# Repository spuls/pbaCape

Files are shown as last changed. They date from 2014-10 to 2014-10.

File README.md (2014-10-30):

pbaCape
=======

BeagleBone Cape for pba ("Platz-Beregnungs-Anlage")

For software see https://github.com/fknittel/pba

## TestBoard
For testing the basic circuit a test layout was developed. It was soldered together and used with one original relay (same as used for the "real" thing).

## Prototype RC1
The RC1 schematics were send of for PCB manufacturing. The bare board was soldered manually. The prototype is still used for the "real" thing. But:
- Some resistor values were choosen borderline. Only 4 out of 6 outputs worked as advertised. (Values corrected in V05.sch)
  Wrong relay behaviour can be seen here: https://www.youtube.com/watch?v=9P7xhbd6JEQ 
  Correctly it should be: https://www.youtube.com/watch?v=5yiceOrfvFM 
- Some GPIOs (P8_39, 41, 43, 45) that were chosen first interfered with "boot"-pins of the BeagelBone. Thus, the board would not boot properly.
  These were manually corrected via wire bridges to be P8_17, 18, 28 and 30 respectively. (Also corrected in V05.sch)
- There is no internet connection (currently). Thus, no time information is available. A real time clock (RTC) was needed. It was manually soldered. 
  (Not yet corrected in schematics.)

## Code
The code here is only for simple testing purposes. It uses PyBBIO (https://github.com/alexanderhiam/PyBBIO/wiki).

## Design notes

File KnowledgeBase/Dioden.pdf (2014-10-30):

ANGEWANDTE ELEKTRONIK | DIODEN | SEITE 1

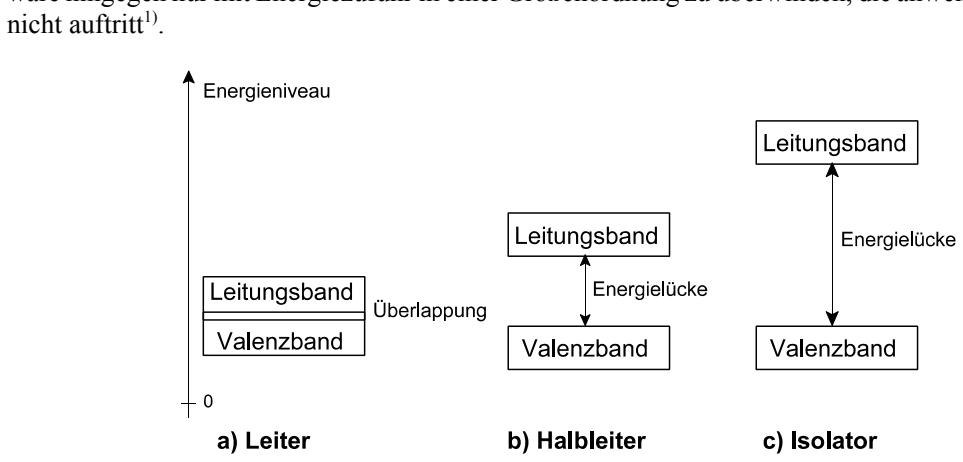
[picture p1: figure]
nicht auftritt¹⁾.

1: Oder – falls doch – zerstörende Wirkungen hätte (Durchschlagen, Durchbrennen).

## 1. Dioden

### 1.1 Grundlagen

Leiter – Halbleiter – Isolatoren
Ein elektrischer Strom kann nur dann fließen, wenn Ladungsträger zur Verfügung stehen. Der elementare Ladungsträger ist das Elektron. Elektronen sind jene Elementarteilchen, die die Kerne der Atome umkreisen. Sind alle Elektronen in den Atomen gebunden, so stehen keine Ladungsträger zur Verfügung, um Strom leiten zu können. Ein solcher Stoff stellt einen idealen Isolator (Nichtleiter) dar. Indem man Energie aufwendet, ist es möglich, Elektronen aus dem Atom herauszulösen und somit als freie Ladungsträger verfügbar zu machen. Das betrifft jene Elektronen, die sich in der der äußeren Schale befinden und die die Bindungen zwischen benachbarten Atomen bewirken (Valenzelektronen). Die Stoffe unterscheiden sich darin, wieviel Energie zugeführt werden muß, um Valenzelektronen freizusetzen. Hierbei gibt es keinen kontinuierlichen Übergang, sondern Bereiche (Bänder), denen verschiedene Energieniveaus zugeordnet sind (Abb. 1.1). Beim Leiter überlappen sich beide Bänder, so daß auch ohne besondere Energiezufuhr stets freie Elektronen zur Verfügung stehen. Bei Halbleitern und Isolatoren sind die Bänder voneinander entfernt (Energielücke). Um Elektronen aus dem Valenzband herauszulösen und in das Leitungsband zu überführen, ist diese Energielücke durch Energiezufuhr zu überwinden. Die schmale Energielücke der Halbleiter kann überwunden werden. Die breite Energielücke der Isolatoren wäre hingegen nur mit Energiezufuhr in einer Größenordnung zu überwinden, die anwendungspraktisch

Abb. 1.1 Valenzband: das Elektron befindet sich in der äußeren Schale und krese um den Atomkern. Leitungsband: das Elektron ist nicht mehr im Atom gebunden, sondern frei beweglich. Es steht somit zur Verfügung, um Strom zu leiten.

Eigenleitung
Die uns interessierenden Halbleitermaterialien sind Kristallstrukturen. Ein absolut reiner Halbleiterkristall, z. B. ein Stück Reinstsilizium, leitet bei tiefen Temperaturen praktisch keinen Strom. Es stehen keine Ladungsträger zur Verfügung, da alle Elektronen in den Atomen des Kristallgitters gebunden sind. Wärme oder Licht versetzen die Atome in Schwingungen. Dadurch werden einige Elektronen aus dem Verband herausgelöst, so daß Strom fließen kann. Die herausgelösten Elektronen hinterlassen buchstäblich "Löcher" (Holes) in den Kristallbindungen. Diese sind logischerweise Träger

ANGEWANDTE ELEKTRONIK | DIODEN | SEITE 2

einer positiven Ladung. Ein solches Loch kann von einem Elektron besetzt werden, das dann seinerseits ein Loch hinterläßt. Den Vorgang, daß ein Elektron eine Loch-Position besetzt, nennt man Rekombination.

Obwohl ein Loch (andere Bezeichnungen: Fehlstelle, Störstelle, Defektelektron) nichts Gegenständliches ist, kann man es als Träger positiver Ladung ansehen und mit den entsprechenden Ladungsträger-Kennwerten rechnen. So entsprechen Masse und Ladungsmenge eines Loches der eines Elektrons (nur hat die Ladungsmenge ein umgekehrtes Vorzeichen). Elektronen fließen von Minus nach Plus, Löcher von Plus nach Minus. Die Bewegungsgeschwindigkeit von Löchern ist aber viel geringer als die von Elektronen (das ist die physikalische Ursache dafür, daß man für NPN-Transistoren weniger Silizium braucht als für PNP-Transistoren mit vergleichbaren Kennwerten).

Dotierung
Um mit Halbleitern Gleichricht- und Verstärkerwirkung zu erbringen, ist die Eigenleitung nicht ausreichend. Man muß vielmehr den Leitungsmechanismus gezielt beeinflussen. Dies erreicht man durch Beimischungen von Atomen anderer Wertigkeit (Dotierung). Hat ein solches Atom eine höhere Wertigkeit, so können nicht alle seine Bindungselektronen in den Kristallverband eingebaut (und somit neutralisiert) werden. Somit ist ein Überschuß an Elektronen vorhanden, der verfügbar ist, um Strom zu leiten (Elektronen- oder N-Leitung). Hat ein solches Atom hingegen eine geringere Wertigkeit, so fehlen an den Bindungsstellen des Kristalls Elektronen. Somit ist ein Überschuß an Löchern vorhanden, der ebenfalls zur Stromleitung nutzbar ist (Löcher- oder P-Leitung). Eine Dotierung, die einen Elektronenüberschuß erzeugt, heißt Donator-Dotierung, eine, die einen Überschuß an Löchern erzeugt, Akzeptor-Dotierung. Die Ladungsträger, die infolge der Dotierung vorherrschen, heißen Majoritätsträger, die jeweils anderen Minoritätsträger. Bei Silizium als Halbleiter-Grundwerkstoff bestehen Donator-Dotierungen aus fünfwertigen Atomen (z. B. Antimon Sb oder Phosphor P) und Akzeptor-Dotierungen aus dreiwertigen (z. B. Bor B oder Gallium Ga). Silizium selbst ist vierwertig. Abb. 1.2 zeigt, wie durch Dotierung einer Kristallstruktur N-leitende und P-leitende Halbleiterschichten erzeugt werden. Abb. 1.3 veranschaulicht das Prinzip der Löcherleitung.

Der PN-Übergang
Ein PN-Übergang entsteht, wenn ein Stück Halbleitermaterial auf einer Seite eine Akzeptor-Dotierung und auf der anderen eine Donator-Dotierung erhält, so daß eine P-leitende Zone einer N-leitenden unmittelbar gegenübersteht (Abb. 1.4). Legt man eine Spannungsquelle mit dem Pluspol an die P-leitende Zone und mit dem Minuspol an die N-leitende, so werden die Elektronen zum Pluspol und die Löcher zum Minuspol fließen (gleichnamige Pole stoßen einander ab; die jeweiligen Majoritätsträger werden also buchstäblich aufeinander zugedrückt). Im eigentlichen Übergangsbereich treffen Elektronen und Löcher aufeinander und rekombinieren. Es fließt also tatsächlich ein Strom. Legt man hingegen die Spannungsquelle mit dem Pluspol an die N-leitende Zone und mit dem Minuspol an die P-leitende, so werden die Majoritätsträger förmlich zu den Anschlüssen der Spannungsquelle hingesaugt (ungleichnamige Pole ziehen einander an). Der eigentliche Übergangsbereich ist somit weitgehend frei von Ladungsträgern, so daß kein nennenswerter Strom fließen kann (Sperrschicht).

ANGEWANDTE ELEKTRONIK | DIODEN | SEITE 3

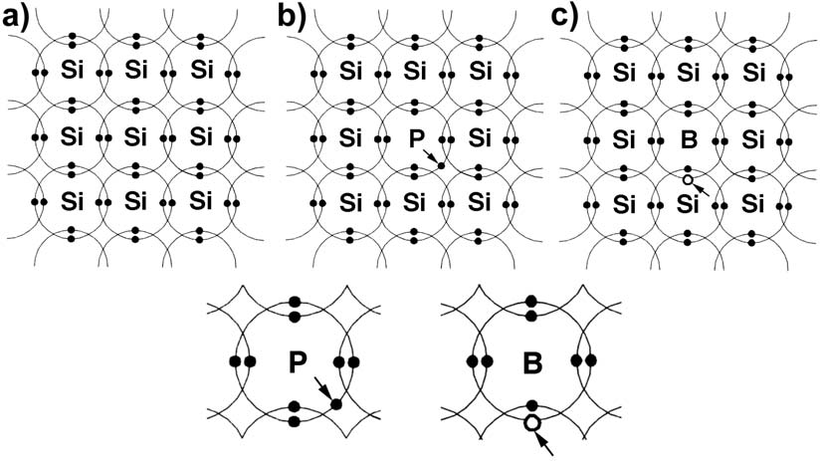
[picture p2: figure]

Abb. 1.2 Dotierung eines Halbleiterkristalls.a) ein reiner Siliziumkristall. Alle Valenzelektronen der Atome sind in Doppelbindungen (kovariante Bindungen) einbezogen. b) N-Leitung durch Einbau eines fünfwertigen Atoms (z. B. Phosphor P), c) P-Leitung durch Einbau eines dreiwertigen Atoms (z. B. Bor B).

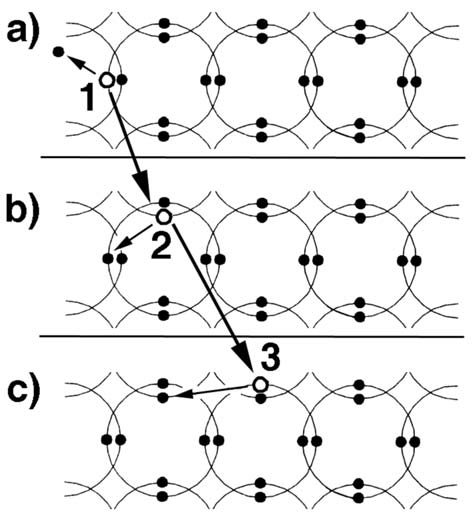
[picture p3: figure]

Abb. 1.3 Prinzip der Löcherleitung. Löcher an sich können sich nicht bewegen – auch hier sind es eigentlich die Elektronen. a), b) und c) zeigen die gleichen Atome zu verschiedenen Zeitpunkten. a) Elektron 1 verläßt seinen Platz in einer Doppelbindung; es ergibt sich das erste Loch. b) Elektron 2 verläßt seinen Platz in einer Doppelbindung und fällt gleichsam in die Position des Lochs 1 (Rekombination). c) Loch 2 wird von Elektron 3 gefüllt, das einerseits seinen Platz in einer Doppelbindung verlassen hat. Infolge dieser Elektronenbewegung scheint es so, als ob ein Loch von Postion 1 über Position 2 nach Position 3 gewandert ist.

ANGEWANDTE ELEKTRONIK | DIODEN | SEITE 4

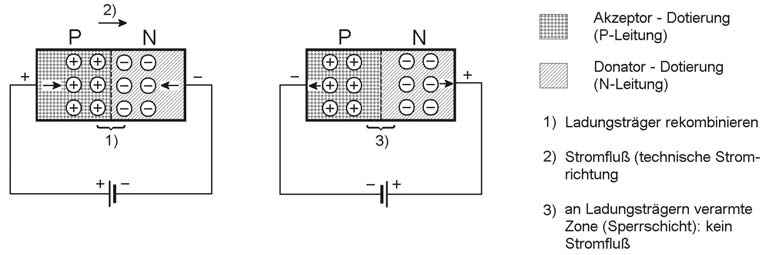
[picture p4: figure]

Abb. 1.4 Der PN-Übergang. Links: Betrieb in Durchlaßrichtung, rechts: Betrieb in Sperrichtung.

### 1.2 Dioden

Dioden sind passive Halbleiterbauelemente mit zwei Anschlüssen. Der eine Anschluß heißt Katode, der andere Anode. Die ideale Diode wirkt wie ein Schalter, dessen Stellung davon bestimmt wird, an welchem der beiden Anschlüsse das positivere und an welchem das negativere Potential anliegt:

- Liegt an der Katode eine negativere und an der Anode eine positivere Spannung an, so ist der Schalter geschlossen: die Diode ist leitend bzw. in Durchlaß- oder Flußrichtung geschaltet; es kommt ein Stromfluß zustande,
- Liegt an der Katode eine positivere und an der Anode eine negativere Spannung an, so ist der Schalter geöffnet: die Diode ist gesperrt bzw. in Sperrichtung geschaltet; es kann kein Strom fließen.

In Kurzform:

- Durchlaßrichtung (Forward Direction) = Minus an Katode, Plus an Anode.
- Sperrichtung (Reverse Direction) = Plus an Katode, Minus an Anode.

Es können verschiedene physikalische Effekte und verschiedene Materialien genutzt werden, um derart wirkende Bauelemente zu schaffen. Die meisten modernen Dioden beruhen jedoch auf dem PN-Übergang (üblicherweise als Sperrschicht bezeichnet) und auf Silizium als Basismaterial. Abb. 1.5 veranschaulicht die Grundlagen.

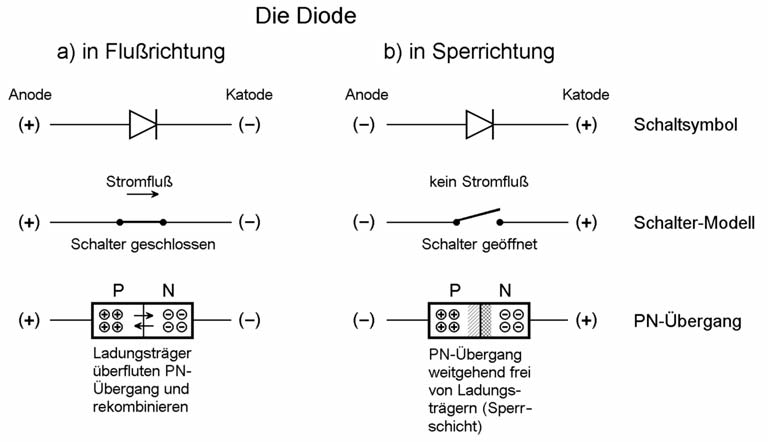
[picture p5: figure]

Abb. 1.5 Die (idealisierte) Halbleiterdiode. Die Anode ist P-leitend, die Katode N-leitend.

ANGEWANDTE ELEKTRONIK | DIODEN | SEITE 5

Die Diode in der Kennlinie
Das einfache Schaltermodell ist für die Praxis zu ungenau. Um die wesentlichen Einzelheiten zu erkennen, müssen wir uns die Strom-Spannungs-Kennlinie der Diode ansehen (Abb. 1.6).

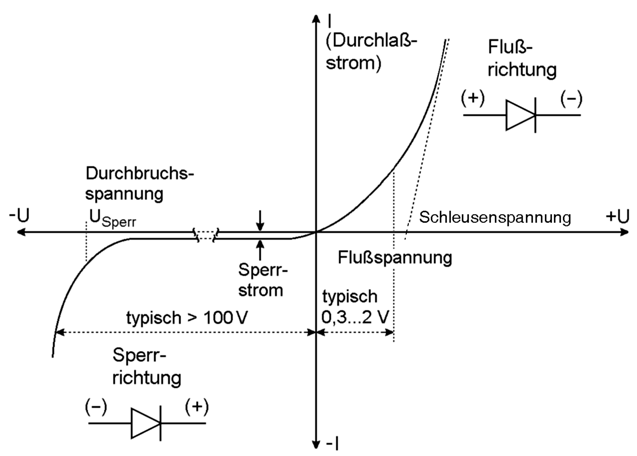
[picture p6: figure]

Abb. 1.6 Diodenkennlinie.

Gleichung der Diodenkennlinie:

I | I | e | Ie D | S

U
nU
S

U
T | T nU =· | -

æ

è

ç
ç

ö

ø

÷
÷ ≈· · | · 1

IS = Sperrsättigungsstrom.

Temperaturspannung U kT
q T =

Bei Zimmertemperatur gilt:

- bei 20 °C: UT . 25 mV,
- bei 25 °C: UT . 26 mV.
k = Boltzmannkonstante 138 10 23 , · - Ws
K

T = Temperatur in K

q = Elementarladung e = 0,16021892 •10⁻¹⁸ C

n = Anpassungsfaktor (Erfahrungswert).

ANGEWANDTE ELEKTRONIK | DIODEN | SEITE 6
| Spannungsbereich | n
Germanium | – | 1
Silizium | U # US | 2
Silizium | U > US | 1

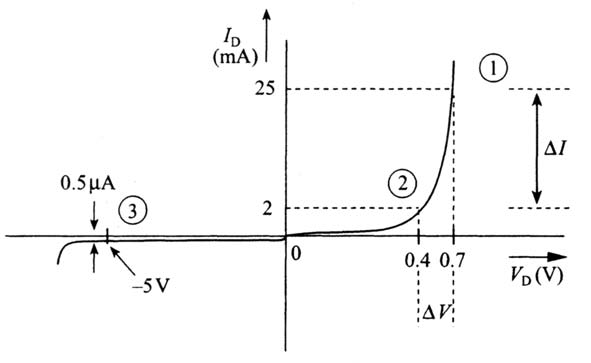
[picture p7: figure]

Abb. 1.7 Der statische Widerstand der Diode.

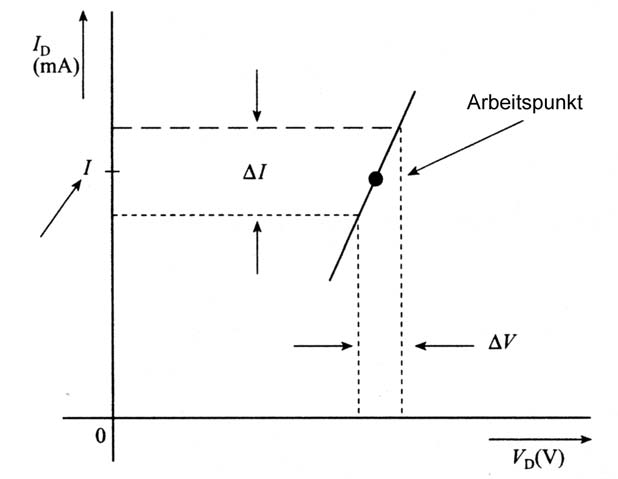
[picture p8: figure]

Abb. 1.8 Der differentielle Widerstand (Wechselstromwiderstand). Er gilt für kleine Änderungen von Spannung und Strom.

Differentieller Widerstand :
dI
dU

e
kT

## Ie S

eU
kT = ··

·

ANGEWANDTE ELEKTRONIK | DIODEN | SEITE 7

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
T = | = | ·
·

≈ ·

1

r

V
I d ≈

0 026 ,

Das entspricht einem differentiellen Leitwert von 38,5 S • I.

Für einen gegebenen Durchlaßstrom IF gilt somit:

- Widerstand = 26 Ω • mA : IF.
- Leitwert = 38,5 mS/mA • IF.

Das entspricht einer Zunahme der Flußspannung um 18 mV bei Verdoppelung und um 60 mV bei Verzehnfachung des Durchlaßstroms (also je Oktave bzw. Dekade).

Temperaturabhängigkeit (Silizium):

- für je 1° Temperaturanstieg fällt die Flußspannung um 2 mV,
- für je 10° Temperaturanstieg verdoppelt sich der Sperrstrom.

Die Durchlaßrichtung
Wenn, von Wert 0 an beginnend, die Spannung an der Anode – bezogen auf die Katode – mehr und mehr positiv wird, fließt zunächst ein nur geringer Strom. Erst nach Überschreiten eines gewissen Spannungswertes Ud steigt die Stromstärke steil an. Dabei nimmt der Spannungsabfall über der Diode kaum zu. Den Wert Ud bezeichnet man als Durchlaß-, Fluß- oder Kniespannung der Diode. Bei geringen Spannungen und Strömen entspricht die Kennlinie in guter Näherung einer Exponentialfunktion.

Die Sperrichtung
Wenn, von Wert 0 an beginnend, die Spannung an der Anode – bezogen auf die Katode – mehr und mehr negativ wird, fließt zunächst ein nur geringer Strom, der Sperrstrom. Erst nach Überschreiten eines gewissen Spannungswertes –Usperr steigt die Stromstärke steil an. Dabei nimmt der Spannungsabfall über der Diode kaum zu. Den Wert Usperr bezeichnet man als maximale Sperrspannung, als Durchbruchspannung oder als Zenerspannung. Bei "gewöhnlichen" Dioden darf dieser Spannungswert im praktischen Betrieb nie erreicht werden. Nur bei den sog. Zenerdioden werden die Durchbruchseffekte praktisch ausgenutzt.

Wir merken uns:

1. Der Stromfluß beginnt bereits bei geringen Spannungen in Flußrichtung. Ein geringe Strom bewirkt auch nur einen geringen Spannungsabfall (exponentielle Abhängigkeit).
2. Über einer Diode, die in Flußrichtung von einem hinreichend starken Strom durchflossen wird, fällt eine Spannung ab, die der Flußspannung entspricht. Der Spannungsabfall nimmt mit wachsender Stärke des Durchlaßstroms nur geringfügig zu (mit anderen Worten: die Diode ist extrem niederohmig, also näherungsweise ein geschlossener Schalter).
3. Durch eine Diode in Sperrichtung fließt nur ein sehr geringer Sperrstrom, der praktisch nicht nennenswert von der anliegenden Sperrspannung abhängt (mit anderen Worten: die Diode ist extrem hochohmig, also näherungsweise ein offener Schalter).
4. Die im Betrieb anliegende Sperrspannung muß stets geringer sein als die maximale Sperrspannung (Durchbruch- oder Zenerspannung).

ANGEWANDTE ELEKTRONIK | DIODEN | SEITE 8

Der Übergang in den Bereich des steilen Anstiegs wird durch Spannungsangaben gekennzeichnet:

- Schwellenspannung (Threshold Voltage VTh) oder Schleusenspannung US: an den steil ansteigenden Bereich der Kennlinie wird eine Tangente angelegt und bis zur Spannungsachse verlängert,
- Flußspannung Ud (Forward Voltage VF): dies ist typischerweise die über der Diode abfallende Spannung, wenn 1/10 des Nennstroms hindurchfließt.

Wie hoch ist die Flußspannung?
Das hängt vom Halbleiter-Basismaterial und von der Ausführung der Diode ab. Anhaltswerte:
- | Siliziumdioden: | 0,5...0,8 V (typisch 0,7 V),
- | Germaniumdioden: | 0,2...0,4 V (typisch 0,35 V),
- Schottky-Dioden: 0,35...0,5 V (typisch 0,45 V).

Abb. 1.9 veranschaulicht die Unterschiede anhand von Kennlinien einer Silizium- und einer Germaniumdiode, die in einem gemeinsamen Koordinatenkreuz dargestellt sind.

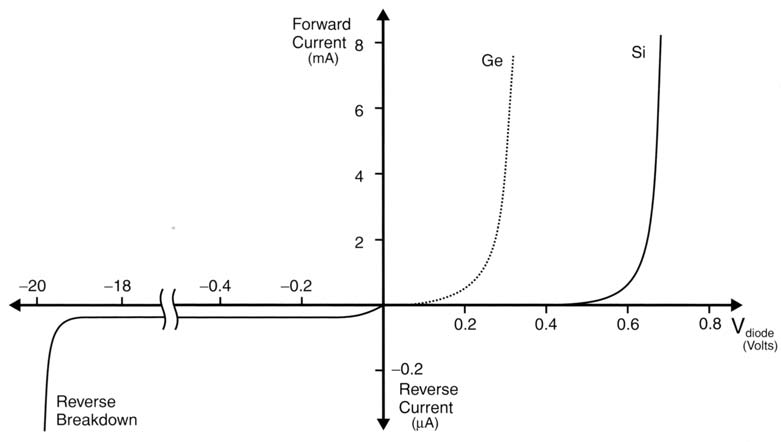
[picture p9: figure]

Abb. 1.9 Kennlinien einer Germanium- und einer Siliziumdiode

In vielen Einsatzfällen ist der typische Wert der Flußspannung eine sinnfällige Größe, um sich die Wirkungsweise von Schaltungen klarzumachen oder um in der Hardware zu messen. Genaugenommen hat die Kennlinie aber in der "Gegend", wo der Durchlaßstrom zu fließen beginnt, keinen plötzlichen Knick. Sie ist vielmehr in charakteristischer Weise gekrümmt. Hierbei gibt es deutliche Unterschiede zwischen den einzelnen Typen. Und genau dieser Verlauf ist bei manchen Anwendungen (z.B. als Leistungsgleichrichter) von besonderer Bedeutung. Deshalb wird in den Datenblättern gelegentlich der genaue Kennlinienverlauf in der Umgebung des Flußspannungs-Wertes graphisch dargestellt (Abb. 1.10).

ANGEWANDTE ELEKTRONIK | DIODEN | SEITE 9

Abb. 1.10 Die Basis-Kollektor-Strecken eines Transistors können als Diode genutzt werden. a) der NPN-Transistor als Verbund zweier Dioden (Ersatzschaltung). b) die Diode zwischen Basis und Kollektor hat geringe Leckströme, aber längere Schaltzeiten. c) die Diode zwischen Basis und Emitter hat besonders kurze Schaltzeiten. Die zulässige Sperrspannung ist aber gering (Richtwert: 5...6 V).

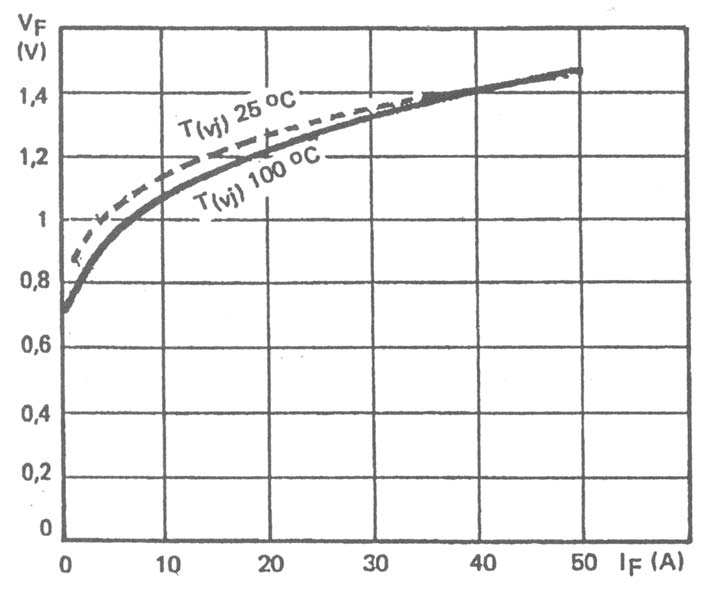
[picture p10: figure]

Abb. 1.11 Spannungsabfall VF in Flußrichtung als Funktion des Durchlaßstroms IF (Gleichrichterdiode BY 233; Quelle: SGS-Thomson).

Man hat hier die Graphik gegenüber der lehrbuchmäßigen Darstellung (z. B. Abb. 1.6) umgedreht, um die Abhängigkeit des Spannungsabfalls vom Strom deutlich herauszustellen (bei Gleichrichteranwen-dungen ist der Stromfluß gegeben, und man will wissen, mit welchem Spannungsabfall bei einer be-stimmten Stromstärke zu rechnen ist).

ANGEWANDTE ELEKTRONIK | DIODEN | SEITE 10

Diodenanwendungen in Embedded Systems
Dioden werden sowohl innerhalb integrierter Schaltungen als auch – in beträchtlichen Stückzahlen – als Einzelbauelemente eingesetzt (Abb. 1.12). In Embedded Systems haben folgende Anwendungsgebiete die größte Bedeutung:
- Gleichrichten von Wechselspannungen,
- Spannungsstabilisierung,
- Begrenzungs- und Schutzfunktionen,
- Ventil- und Schaltfunktionen,
- optische Wirkungen (Licht aussenden (Leuchtdioden), Licht empfangen (Photodioden)).

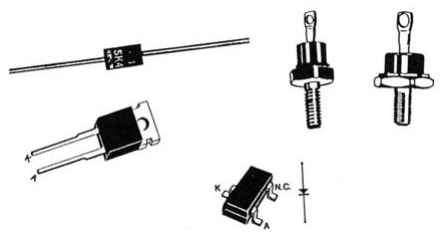
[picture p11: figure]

Abb. 1.12 Dioden.

Anschlußkennzeichnung
Dioden in zylindrischen Bauformen haben einen Ring am Gehäuse, der die Katode kennzeichnet. Bei manchen Dioden in Plastikgehäusen (mit beiden Anschlüssen nebeneinander) sind die Anschlußdrähte unterschiedlich lang. Der kürzere ist die Katode. Ist die Anschlußbelegung nicht eindeutig erkennbar, hilft nur Messen.

Dioden für Kühlkörpermontage
Sind beide Anschlüsse gegenüber den Montage-Vorkehrungen (Schraubgewinde, Platte mit Befestigungsbohrung o. ä.) völlig isoliert, ist nichts zu beachten. Ansonsten: es gibt "katodenverbundene" und "anodenverbundene" Typen (der Kühlkörper ist dann – wenn nicht durch Zwischenlagen, Montage mit Kunststoffschrauben usw. isoliert – entweder mit der Katode oder der Anode verbunden). Meistens hat die Vorzugsausführung die Katode am Gehäuse. Praktisch alle einschlägigen Typen werden aber auch mit der Anode am Gehäuse geliefert. Achten Sie also auf die genauen Typen- und Bestellnummern! (So sind zum Aufbau von Brückengleichrichtern je zwei Dioden in jeder Bauform zweckmäßig.)

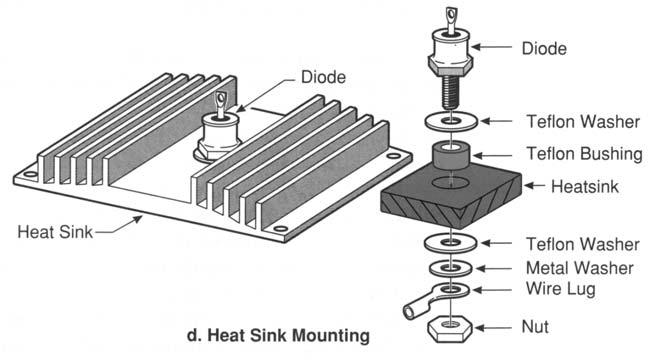
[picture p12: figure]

Abb. 1.13 Kühlkörpermontage.

ANGEWANDTE ELEKTRONIK | DIODEN | SEITE 11

Mehrfachdioden
Mehrfachdioden-Bauelemente enthalten mehrere unabhängige Dioden oder Diodenkombinationen, die für bestimmte Anwendungen gleichsam vorgefertigt sind (als Schutzdioden-Anordnungen, als Zweiweg-oder Brückengleichrichter usw.).

Dioden im Schaltplan
In Abb. 1.14 sind die üblichen Schaltsymbole für Dioden zusammengestellt. Beachten Sie die bildhafte Symbolik: der Querstrich ist die Katode, und der Pfeil zeigt in Flußrichtung, wenn die Anode an positiverer Spannung liegt (technische Stromrichtung von Plus nach Minus).

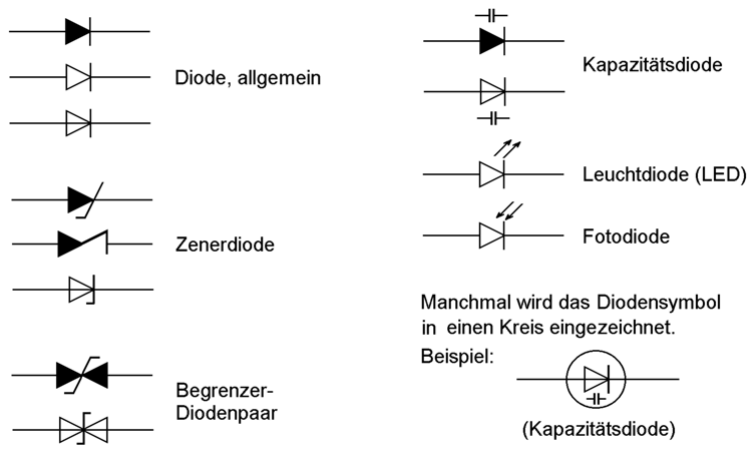
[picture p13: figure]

Abb. 1.14 Schaltsymbole für Dioden.

### 1.3 Siliziumdioden

Statische Kennwerte
Das Strom-Spannungs-Verhalten der gewöhnlichen"Siliziumdiode ist aus Kennlinien ähnlich Abb. 1.9 und 1.11 ersichtlich. Im folgenden geben wir zunächst einen Überblick über die Kennwerte, die wir bisher besprochen haben und nennen die in Datenblättern üblichen Bezeichnungen.

Maximaler Durchlaßstrom (Forward Current IF)
Zu Schalt- und Kleinleistungsdioden findet man oft nur eine einzige Durchlaßstromangabe. Leistungsgleichrichter werden hingegen durch mehrere Werte charakterisiert. Wir nennen hier die wichtigsten:
- Dauergrenzstrom (Average Forward Current IFAV): der höchste zulässige Mittelwert eines sinusförmigen Durchlaßstromes im Dauerbetrieb (bezogen auf einen Frequenzbereich von 50...60 Hz).
- Dauergleichstrom (IFDC): der höchste Gleichstrom, der in Durchlaßrichtung fließen darf. Faustregel: IFDC = 1,5 IFAV.
- höchster periodischer Durchlaßstrom (Repetitive Peak Forward Current IFRM): der höchste zulässige Augenblickswert des Durchlaßstromes, der periodisch wiederholt auftreten darf (die Höchstdauer der Erregung steht im Datenblatt; typisch sind $ 10 μs).

ANGEWANDTE ELEKTRONIK | DIODEN | SEITE 12

2: Exponentielles Wachstum. Richtwert: bei geringen Strömen um 60...120 mV/Dekade (Verzehnfachung der Stromstärke).

3: Ein typischer Datenblattwert: Spannungsabfall bei 10% des maximalen Durchlaßstroms.

- Stoßstromgrenzwert (Surge Non Repetitive Forward Current IFSM): der höchste zulässige Augenblickswert des Durchlaßstromes, der bei nicht periodischem Auftreten zulässig ist (wie der Bezugs-Stromstoß aussieht, steht im Datenblatt; typisch ist eine Sinus-Halbwelle von 10 ms Dauer).

Flußspannung (Forward Voltage VF)
Die Flußspannung (Pauschalwert für SI-Dioden um 0,7 V) ist – genau genommen – stromabhängig²⁾. Die Datenblätter nennen deshalb meist nur 1 oder 2 Werte im Tabellenteil³⁾ und geben genauere Abhängigkeiten graphisch an (vgl. Abb. 1.11). "Dicke" Leistungsgleichrichter für Ströme von 100 A und mehr haben Flußspannungen um 1,5... > 2 V.

Temperaturgang der Flußspannung bei konstantem Duchlaßstrom: etwa – 2 mV/K (Richtwert). Liegt eine konstante Spannung an, so steigt der Durchlaßstrom exponentiell mit der Temperatur.

Sperrstrom (Reverse Current IR)
Der Sperrstrom von Siliziumdioden ist sehr gering und hängt im wesentlichen von der Betriebstemperatur ab (Bereich von wenigen nA bis zu einigen μA bei stark belasteten Leistungsgleichrichtern; beispielsweise 50 μA Sperrstrom und 80 A Durchlaßstrom). Genauere Abhängigkeiten werden üblicherweise graphisch dargestellt.

Temperaturgang des Sperrstroms: Verdoppelung bei 10K Temperaturerhöhung ( ).

Maximale Sperrspannung (Peak Reverse Voltage VR)
Bei Schalt- und Kleinleistungsdioden reicht meist ein einziger Wert für die Sperrspannung. Bei Leistungsgleichrichtern sind hingegen – gemäß den verschiedenen Betriebsfällen – mehrere Sperrspannungsangaben erforderlich.
- höchste periodische Spitzensperrspannung (Repetitive Peak Reverse Voltage VRRM): der höchste Augenblickswert der Sperrspannung, der periodisch wieder-holt auftreten darf.
- höchste Stoßspitzensperrspannung (Non Repetitive Peak Reverse Voltage VRSM): der höchste Augenblickswert der Sperrspannung, der bei nicht periodischem Auftreten zulässig ist (maximale Dauer: 10 ms).
- empfohlene Anschlußspannung (VRMS): Nenn-Effektivwert der anliegenden sinusförmigen Wechselspannung (bei Gleichrichter-Anwendungen).
- Faustregel: VRMS = 0,5 VRRM.

Abb. 1.15 veranschaulicht, welche Sperrspannung die Diode im einfachen Spitzenwertgleichrichter

Abb. 1.15 Der ungünstigste Betriebsfall. Der Kondensator ist auf den Spitzenwert aufgeladen, und in Sperrichtung liegt der entgegengesetzt gepolte Spitzenwert an.

ANGEWANDTE ELEKTRONIK | DIODEN | SEITE 13
Es gilt also: | V | U R | SS ≥

Bei sinusförmigem Wechselspannungsverlauf:
V | V R | RMS ≥ 28, ·

Verlustleistung (Power Dissipation Ptot)
Die Verlustleistung ergibt sich - näherungsweise gerechnet - als Produkt von Durchlaßstrom und Flußspannung: Ptot = IFAV @ VF. Angaben zu Gehäusetemperatur und Anforderungen an die Kühlung beachten!

Das dynamische Verhalten
Wenn eine Diode umgepolt wird, laufen Vorgänge ab, die Zeit erfordern. Betrachten wir dazu nochmals die einfachen Skizzen zum PN-Übergang in Abb. 1.4. Nehmen wir an, die Diode werde in Sperrichtung betrieben. Dann ist der eigentliche PN-Übergang (die Sperrschicht) nahezu frei von Ladungsträgern. Nun polen wir die Spannung um. Jetzt muß die Diode leiten. Aber dazu müssen erst einmal die Ladungsträger zur Sperrschicht kommen. Diesen Effekt bezeichnet man als Durchlaßträgheit, und der entsprechende Zeit-Kennwert heißt Durchlaßverzögerungszeit (Forward Recovery Time tfr). Bei Schalter-Anwendungen kann es sein, daß man mit dieser Verzögerung rechnen muß; bei Gleichrichter-Anwendungen ist sie weniger von Bedeutung. Schließlich geschieht nicht mehr, als daß die Sperrwirkung erst einige ns nach dem Umpolen aufgehoben wird.

Was passiert aber im umgekehrten Fall? – Die Diode leitet, folglich ist die Sperrschicht mit Ladungsträgern regelrecht überflutet. Nun wird auf "Sperren" umgepolt. Zunächst sind aber noch Ladungsträger in der Sperrschicht. Die Folge: eine gewisse Zeit kann ein recht starker Strom (theoretisch: in Höhe des Durchlaßstromes) in Sperrichtung fließen! Erst dann, wenn sich die Ladungsträger aus der Sperrschicht zurückgezogen haben (man spricht hier bildhaft vom Ausräumen), ist die Diode wirklich gesperrt. Diesen Effekt bezeichnet man als Sperrträgheit; der Zeit-Kennwert heißt Sperrverzögerungszeit (Backward Recovery Time trr). Abb. 1.16 veranschaulicht das beschriebene Verhalten.

Es ist offensichtlich, daß die halbe Periodendauer einer gleichzurichtenden Wechselspannung viel länger sein sollte als die Sperrträgheit. Sind Wechselspannungen höherer Frequenz gleichzurichten (Spannungswandler, Schaltnetzteile), braucht man Dioden mit besonders geringer Sperrverzögerungszeit (Fast Recovery Diodes). Man erreicht dies durch besondere Gestaltung der Sperrschicht. (So liegt es nahe, die Sperrschicht vergleichsweise hochohmig auszulegen, so daß weniger Ladungsträger auszuräumen sind.)

Orientierungswerte:
Bei modernen Leistungsgleichrichtern liegt tfr um 10 ns und trr um 200...50 ns.

Abb. 1.17 zeigt die Verbessserung, die sich ergibt, wenn weniger Ladungsträger auszuräumen sind.

Es ist aber auch erkennbar, was es bedeutet, wenn die Sperrschicht sehr schnell ausgeräumt wird: der Ausräum-Strom bricht schlagartig zusammen. Und das hat zur Folge, daß kräftige Spannungsspitzen induziert werden, die auf jeden Fall Störungen hervorrufen, wenn nicht gar den Totalausfall der Diode. Der Ausweg: Man muß nicht nur die Ausräumzeit verkürzen (Fast Recovery), sondern auch dafür sorgen, daß das Ausräumen "sanft" abläuft (Soft Recovery; Abb. 1.18).

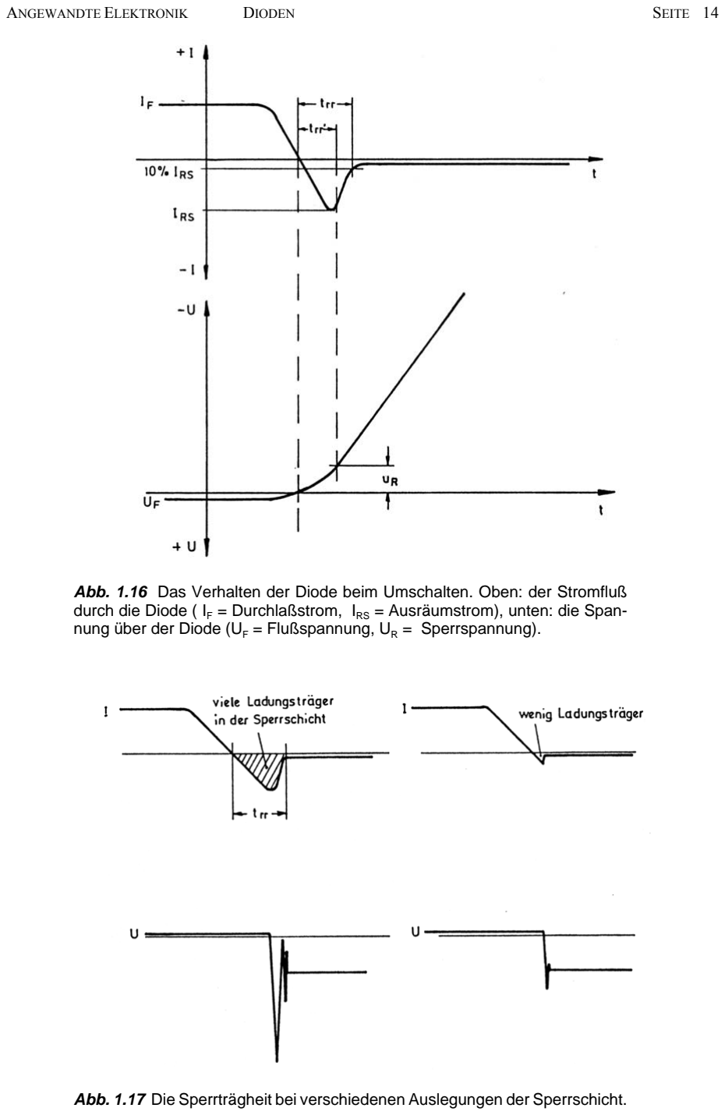
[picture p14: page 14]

ANGEWANDTE ELEKTRONIK | DIODEN | SEITE 14

Abb. 1.16 Das Verhalten der Diode beim Umschalten. Oben: der Stromfluß durch die Diode ( IF = Durchlaßstrom, IRS = Ausräumstrom), unten: die Spannung über der Diode (UF = Flußspannung, UR = Sperrspannung).

Abb. 1.17 Die Sperrträgheit bei verschiedenen Auslegungen der Sperrschicht.

ANGEWANDTE ELEKTRONIK | DIODEN | SEITE 15

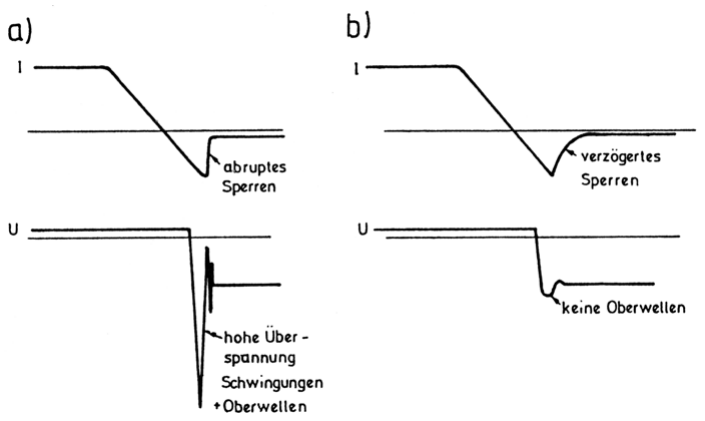
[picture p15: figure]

Abb. 1.18 Der Verlauf des Ausräumstroms. (a) steiler, b) verzögerter Abfall (Soft Recovery).

### 1.4 Schottky-Dioden

Schottky-Dioden beruhen auf einem Metall-Halbleiter-Übergang. Sie haben gegenüber gewöhnlichen Siliziumdioden folgende Besonderheiten:

- Die Flußspannung ist etwa auf die Hälfte reduziert (typisch 0,35...0,45 V; vgl. Abb. 1.19a).
- Der Sperrstrom (Leckstrom) ist höher (vgl. Abb. 1.19b).
- Der Ausräumstrom ist praktisch vernachlässigbar (vgl. Abb. 1.19c).
- Die Sperrschichtkapazität ist deutlich geringer (wenige pF) und kaum spannungsabhängig (vgl. Abb. 1.19d).
- Die Durchlaß- und Sperrverzögerungszeiten sind sehr gering. Man gibt meist nur einen Wert als "Schaltzeit" τ an; Größenordnung: 100 ps. Achtung: einige Zeit nach dem Umschalten in die Sperrichtung können noch schwache Restströme fließen (z. B. einige μA für etwa 1μs). Die Ursache: ein parasitäter pn-Übergang, der dem eigentlichen Schottky-Übergang parallelliegt.

Abb. 1.19 veranschaulicht diese Unterschiede anhand von Kennlinien und Werteverläufen (die 1N1418 ist eine "Wald-und-Wiesen"-Siliziumdiode, die BAR- und BAT-Typen sind Schottky-Dioden).

### 1.5 Kapazitätsdioden

Eine in Sperrichtung betriebene Diode ist praktisch ein Kondensator, dessen Dielektrikum die Sperrschicht ist. Weshalb? – Zwischen Katode und Anode liegt eine Spannung, es fließt aber (fast) kein Strom: die Sperrschicht wirkt als Isolator. Die tatsächliche Dicke der Sperrschicht hängt von der anliegenden Sperrspannung ab. Je höher die Spannung, um so dicker die Sperrschicht bzw. das Dielektrikum (Abb. 1.20). Das heißt, die Sperrschichtkapazität kann durch die Sperrspannung verändert werden. Kapazitätsdioden (Abstimmdioden, Varicaps, Varaktoren) sind ausdrücklich für diese Nutzungsweise entwickelt worden. Abb. 1.21 zeigt die Sperrschichtkapazität als Funktion der Sperrspannung für verschiedene Diodentypen (daraus geht auch die typische Größenordnung der Sperrschichtkapazität hervor).

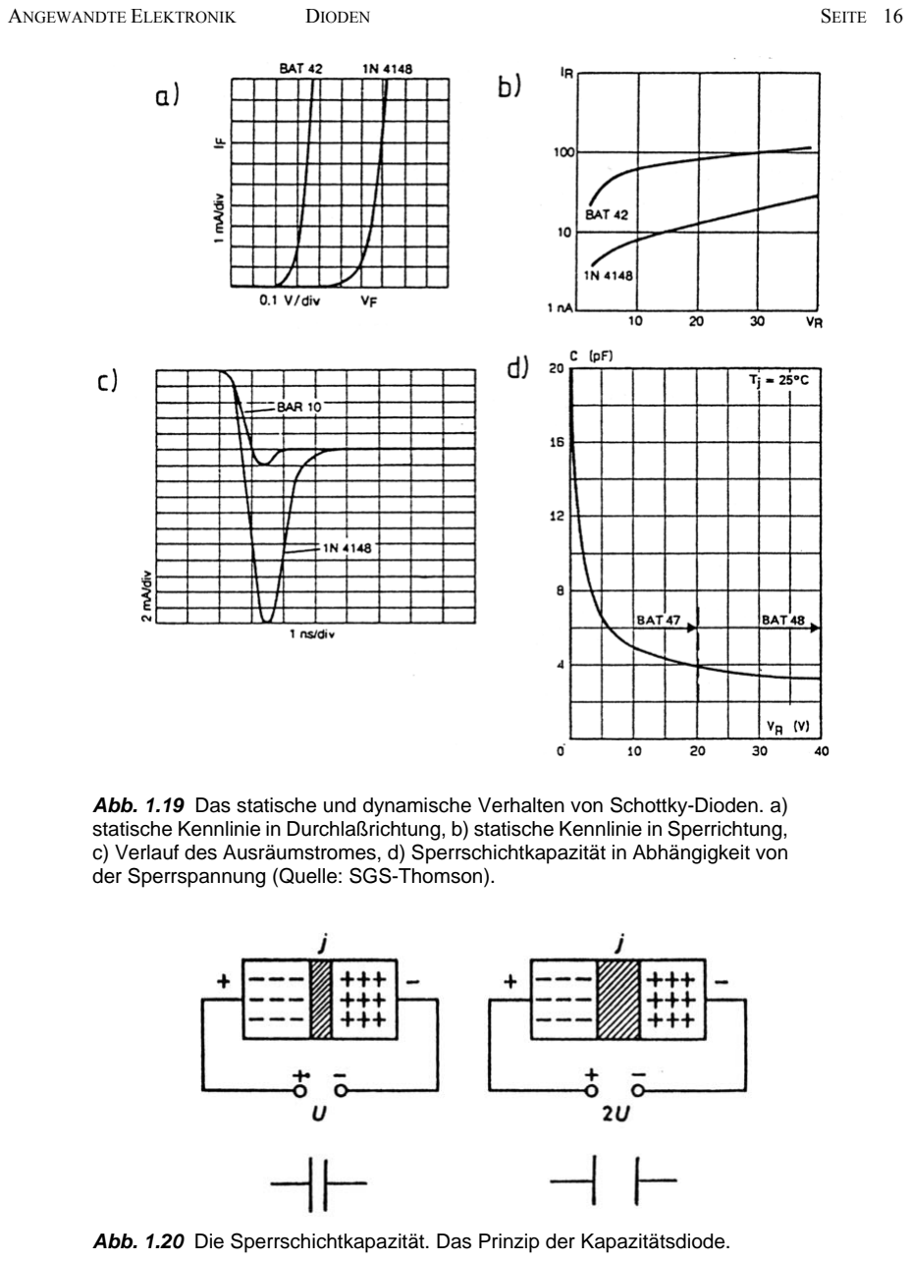
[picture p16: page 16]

ANGEWANDTE ELEKTRONIK | DIODEN | SEITE 16

Abb. 1.19 Das statische und dynamische Verhalten von Schottky-Dioden. a) statische Kennlinie in Durchlaßrichtung, b) statische Kennlinie in Sperrichtung,
c) Verlauf des Ausräumstromes, d) Sperrschichtkapazität in Abhängigkeit von der Sperrspannung (Quelle: SGS-Thomson).

Abb. 1.20 Die Sperrschichtkapazität. Das Prinzip der Kapazitätsdiode.

ANGEWANDTE ELEKTRONIK | DIODEN | SEITE 17

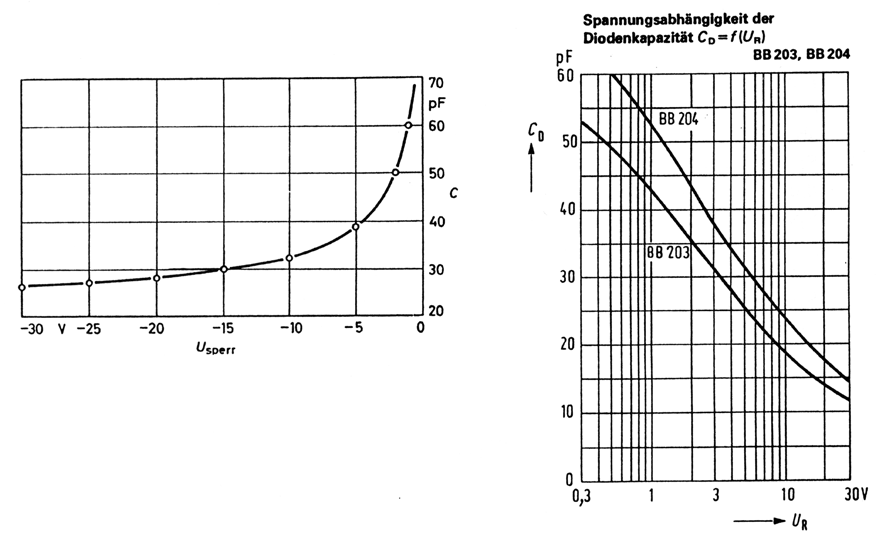
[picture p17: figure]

Abb. 1.21 Die Sperrschichtkapazität in Abhängigkeit von der Sperrspannung. Links: linearer, rechts: logarithmischer Maßstab (Quellen: AEG-Telefunken, Sie-mens).

Abb. 1.22 zeigt, wie man eine Kapazitätsdiode einsetzen kann, um einen Schwingkreis abzustimmen.

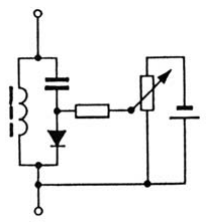
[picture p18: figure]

Abb. 1.22 Schwingkreis-Abstimmung mittels Kapazitätsdiode.

### 1.6 Zenerdioden

Zenerdioden werden in Sperrichtung betrieben, und zwar im Bereich ihrer Durchbruchspannung. Die Durchbruchspannung der üblichen Siliziumdioden liegt in einer Größenordnung von 100 V und mehr, und man ist bestrebt, diese so hoch wie möglich zu halten. Zenerdioden sind hingegen für praktisch brauchbare Durchbruchspannungen (Zenerspannungen) entwickelt worden. Sie dienen zur Spannungsstabilisierung und zu Schutzzwecken. Zenerdioden gibt es mit Zenerspannungen zwischen etwa 1,8 und ca. 270 V, wobei die Nennwerte typischerweise gemäß einer E-Reihe gestaffelt sind. Abb. 1.23 zeigt Sperr- und Durchlaßkennlinien typischer Zenerdioden.

Durchbrucheffekte
Je höher die Sperrspannung, um so mehr werden die Ladungsträger aus dem Bereich des PN-Übergangs förmlich zu denn Anschlüssen hin abgesaugt (vgl. Abb. 1.4). Hohe Sperrspannung bedeutet aber auch hohe Feldstärke. Von einem gewissen Spannungswert an wird die Feldstärke so hoch, daß Elektronen aus ihren

ANGEWANDTE ELEKTRONIK | DIODEN | SEITE 18

Bindungen im Halbleitermaterial gerissen werden und somit als freie Ladungsträger zur Verfügung stehen. Die Folge: der Widerstand sinkt beträchtlich, und der Sperrstrom nimmt schlagartig zu (Durchbruch). “Zenerdiode” (Z-Diode) ist die Allgemeinbezeichnung. Tatsächlich werden zwei Durchbruchseffekte ausgenutzt:

- Der eigentliche Zener-Effekt. Tritt in dünnen, hochdotierten Sperrschichten bei vergleichsweise geringen Sperrspannungen (ca. 5...6 V) auf. Temperaturkoeffizient negativ.
- Der Avalanche-Effekt (Lawinendurchbruch).Tritt in dickeren Sperrschichten bei höheren Sperrspannungen (ab etwa 6 V) auf. Temperaturkoeffizient positiv.

Temperaturkoeffizient: etwa 0,1...0,001 V/K. ±

Der Zener-Effekt ist “schlechter” als der Avalanche-Effekt (Durchbruchskennlinie nicht so steil, schlechterer TK).

Im Bereich um 5 V (4...7 V) werden beide Effekte wirksam. Somit heben sich die Temperaturgänge weitgehend auf; es ergibt sich ein sehr geringer Temperaturkoeffizient. Anwendung: Referenzspannungsquellen. (Bauelemente mit eingebauter Temperaturkonstanthaltung: 0,5...1 ppm/K; Langzeitstabilität 5...10 ppm/K über 1000 h.) Solche Bauelemente vertragen aber nur schwache Ströme (Richtwert: ca. 10 mA). Sie sollten zudem näherungsweise mit ihrem Nennstrom betrieben werden, sonst bringen sie nicht die Genauigkeit, die im Datenblatt versprochen wird.

Achtung: Zenerdioden halten keine übermäßige Strombelastung über längere Zeit aus. Derating-Kurven beachten!

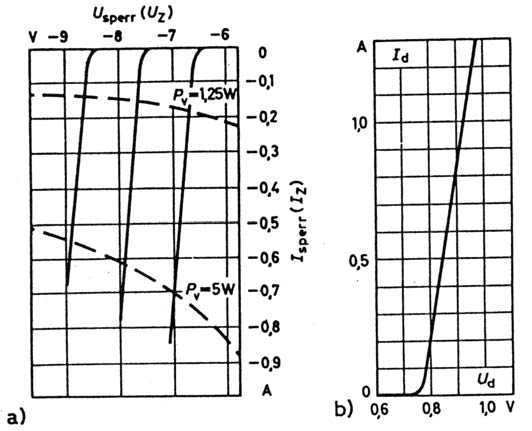
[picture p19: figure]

Abb. 1.23 a) Sperr- und b) Durchlaßkennlinien typischer Zenerdioden

Datenblattwerte
Die wichtigsten Kennwerte sind die Zenerspannung, der minimale Zenerstrom und die maximale Verlustleistung. Viele Datenblätter sind ausgesprochen knapp gehalten. Abb. 1.24 veranschaulicht, was die Werte von Zenerstrom und Zenerspannung typischerwese bedeuten. Die Abbildungen 1.25 bis 1.30 zeigen Datenblattauszüge.

ANGEWANDTE ELEKTRONIK | DIODEN | SEITE 19

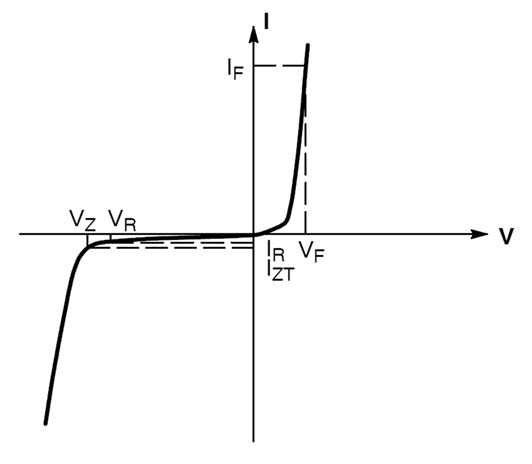
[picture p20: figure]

Abb. 1.24 Zenerstrom und Zenerspannung (Quelle: ON Semiconductor).

Der Teststrom IZT
Die typische Zenerstromangabe betrifft die minimale Stromstärke, bei der über der Zenerdiode eine Zenerspannung im Bereich der Datenblattwerte abfällt; mit anderen Worten, es ist der Strom, mit dem die Zenerspannung abgeprüft wird (Teststrom).

Der maximale Zenerstrom IZM
Das ist die Stromstärke, die die Zenerdiode auf Dauer aushält (Derating für höhere Umgebungstemperaturen beachten!). Manche Datenblätter enthalten solche Werte, ander nicht. Dann ist der maximale Zenerstrom aus der Verlustleistungsangabe zu berechnen:
I P

V ZM

| V Zmax

=

PV = Verlustleistung laut Datenblatt, VZmax = die jeweils maximale Zenerspannung.

Richtwerte zum minimalen Zenerstrom
Welcher Strom muß mindestens durch die Zenerdiode fließen, damit die Zenerspannung sicher im Bereich der Datenblattwerte liegt? Der Datenblattwert ist der oben genannte Teststrom IZT.

Ist IZT nicht bekannt oder geht es nur um Überschlagsrechnungen zwecks Vorauswahl von Bauelementen, kann man ansetzen:
I | I Zmin | ZM ≈ 0 2 0 25 , ... , ·
I | I Zmax | Zmin = | · 45 ...

Für sehr überschlägige Rechnungen genügt gelegentlich auch ein Faktor von 0,1 bzw. 10.

Je stärker der Strom, desto weiter liegt der Arbeitspunkt im steilen Bereich der Kennlinine, desto besser die Spannungsstabilisierung.

ANGEWANDTE ELEKTRONIK | DIODEN | SEITE 20

Was spricht aber dagegen, den Zenerstrom dem zulässigen Maximum (IZM) anzunähern?

- Die Tatsache der Stromaufnahme an sich (Verlustleistung).
- Die Erwärmung der Zenerdiode (Temperaturgang).

Wo der Durchbruch einsetzt
Der Übergang vom Sperr- zum Durchbruchsbereich wird gelegentlich durch Angabe eines sog. Kniestroms IZK charakterisiert.

Die Zenerdiode in Flußrichtung
Sie verhält sich im Grunde wie eine gewöhnliche Siliziumdiode. Manche Typen weisen aber eine höhere Flußspannung auf (vgl. Abb. 1.26).

Der differentielle oder dynamische Widerstand rZ
Dieser Datenblattwert gibt die Steigung der Kennlinie an:

r

U
I Z

Z

Z

= Δ
Δ

Hieraus ergibt sich die maximale Änderung der Zenerspannung gemäß
ΔU | r | I Z | Z | Z = · Δ

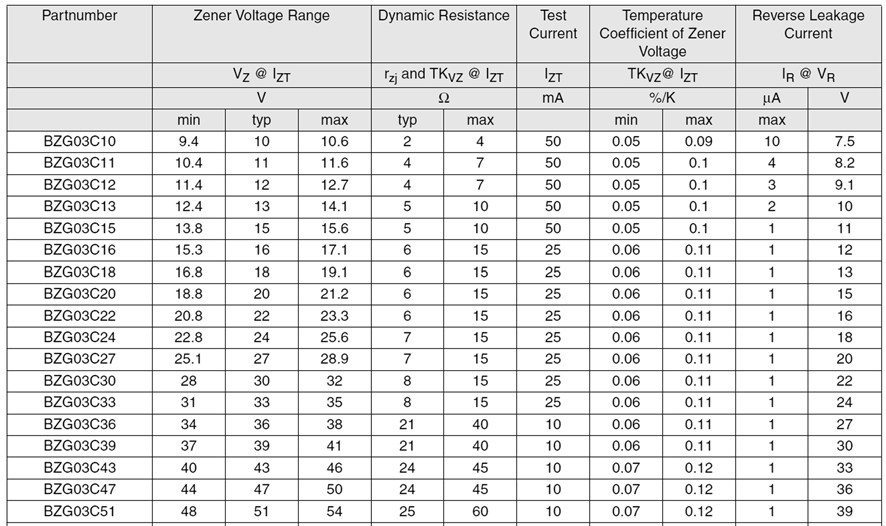
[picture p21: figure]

Abb. 1.25 Datenblattbeispiel 1 (Quelle: Vishay).

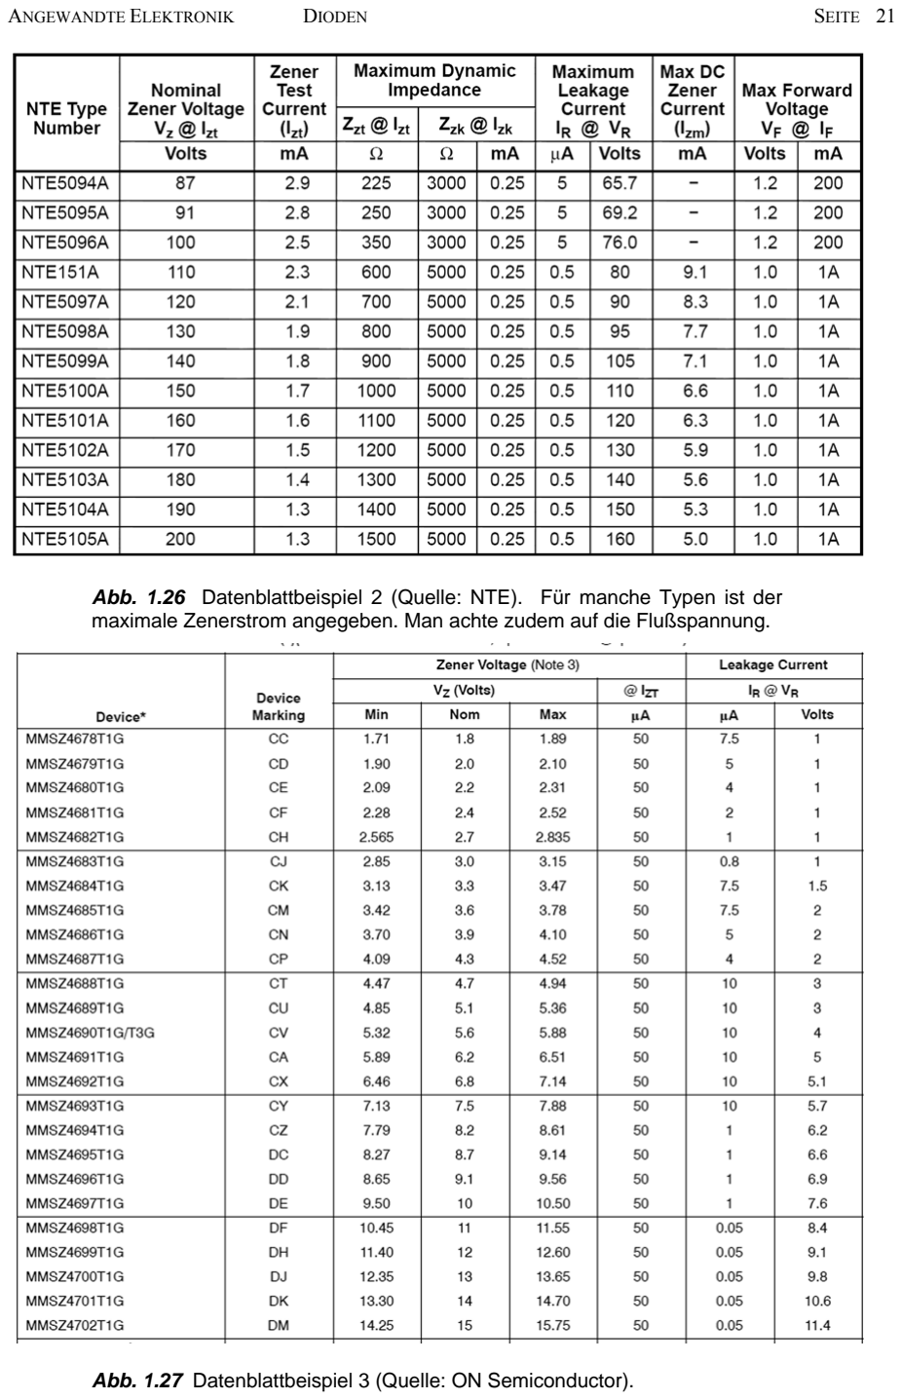
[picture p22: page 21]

ANGEWANDTE ELEKTRONIK | DIODEN | SEITE 21

Abb. 1.26 Datenblattbeispiel 2 (Quelle: NTE). Für manche Typen ist der maximale Zenerstrom angegeben. Man achte zudem auf die Flußspannung.

Abb. 1.27 Datenblattbeispiel 3 (Quelle: ON Semiconductor).

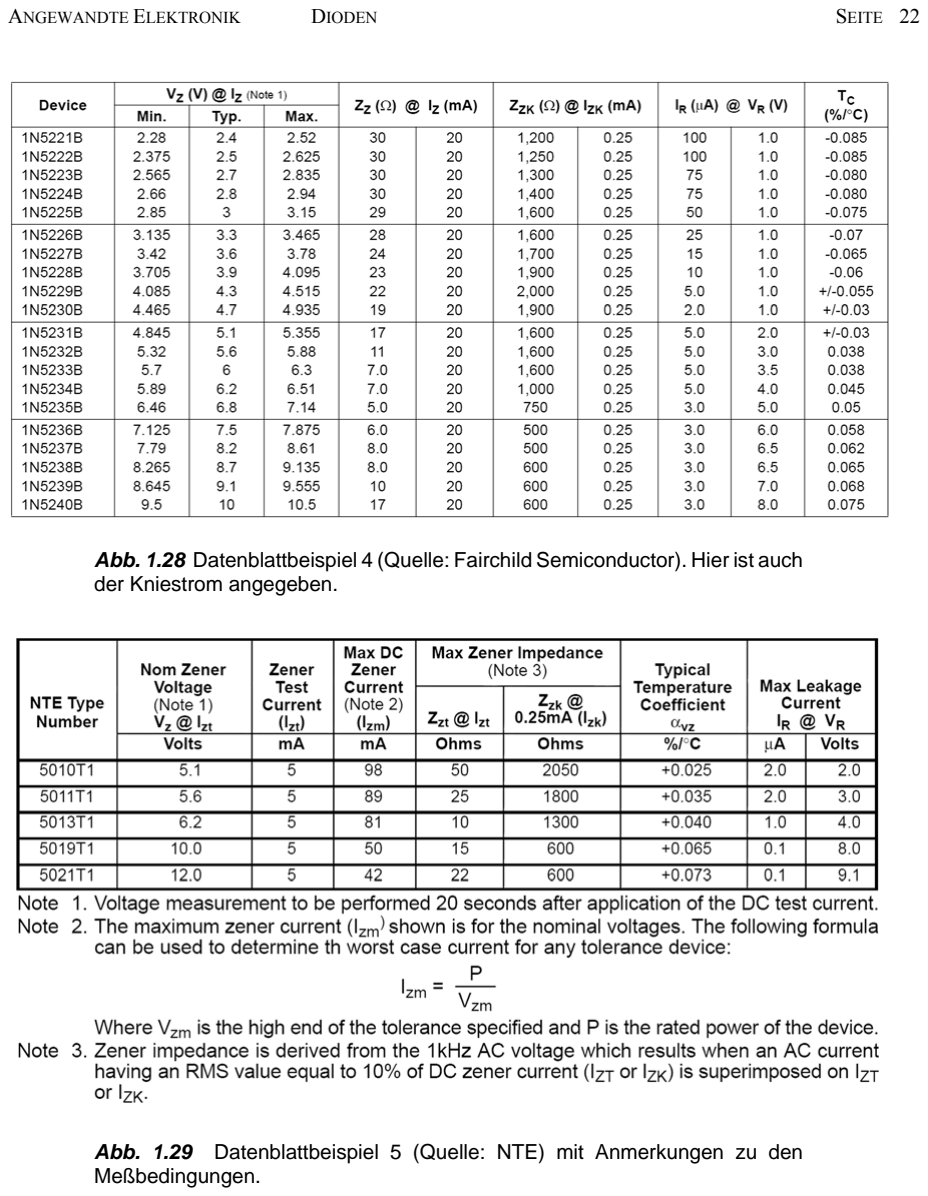
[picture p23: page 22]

ANGEWANDTE ELEKTRONIK | DIODEN | SEITE 22

Abb. 1.28 Datenblattbeispiel 4 (Quelle: Fairchild Semiconductor). Hier ist auch der Kniestrom angegeben.

Abb. 1.29 Datenblattbeispiel 5 (Quelle: NTE) mit Anmerkungen zu den Meßbedingungen.

ANGEWANDTE ELEKTRONIK | DIODEN | SEITE 23

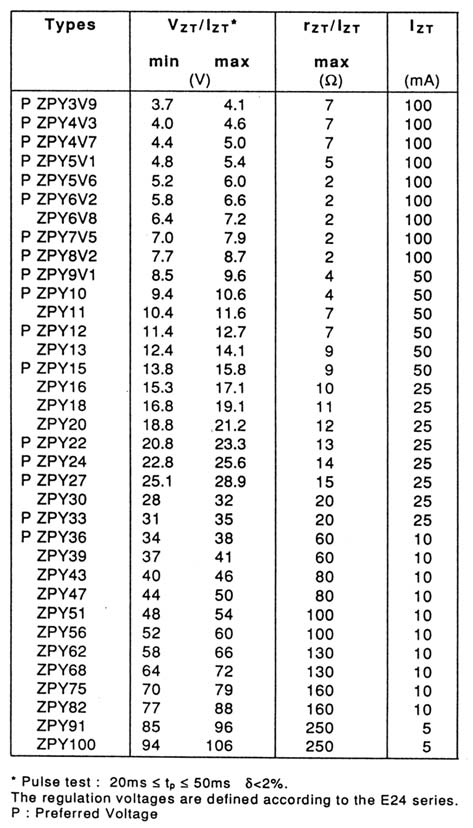
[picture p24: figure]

Abb. 1.30 Datenblattbeispiel 6 (Quelle: SGS-Thomson).

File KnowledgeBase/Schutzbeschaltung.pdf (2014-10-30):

E–Labor | Schutzbeschaltungen | 1

Höhere Technische
Bundes-, Lehr- u. Versuchsanstalt (BULME) Graz –
Gösting

Abgabedatum:

Elektrotechnisches Laboratorium | Jahrgang: | 2004/05
| Gruppe: 3
Name: Schriebl, Forjan, Schuster | Übungstag: 15.4.2005

### 10. Aufgabe: Schutzbeschaltung beim Schalten induktiver Lasten

## 1 Aufgabenstellung

Beim Abschalten induktiver Lasten muss dafür Sorge getragen werden, dass die in der Spule induzierten Spannung nicht Größenordnungen erreicht, die zum Ausfall von Bauteilen (Transistor) führen können. Als Schutzmaßnahmen sollen die Verwendung von Freilaufdioden und eine RC-Beschaltung untersucht und anhand von Oszillogrammen dokumentiert werden. Die Strommessung kann entweder über einen Trennverstärker oder durch Differenzbildung der Spannung am Shunt erfolgen.

Ohne Schutzbeschaltung:

Die Spannung Uce und der Kollektorstrom sind mit dem Oszilloskop aufzunehmen. Um einen Ausfall des Transistors zu verhindern ist ein Varistor zwischen Kollektor und Emitter geschaltet. Ohne dieses Bauteil würde Uce wesentlich höherer Werte erreichen.

Freilaufdiode

Beim Abschalten kann der Strom über die Freilaufdiode weiter fließen und ausklingen.
Der Abschaltvorgang ist durch die Aufnahme von Uce und des Stroms durch die Diode in einem Oszillogramm zu dokumentieren.

RC Beschaltung

Durch die RC Beschaltung kann der Strom in einer gedämpften Schwingung ausklingen. Aus der theoretischen Untersuchung ergeben sich folgende drei möglichen Varianten für das Schwingverhalten, wenn man für Rges die Summe aller ohmschen Widerstände einsetzt (Rges=RL+RShunt+R):

L | LC
RGes | 1
2

ñ

aperiodischer Fall (stark gedämpft)

L | LC
RGes | 1
2

=

aperiodischer Grenzfall

E–Labor | Schutzbeschaltungen | 2
L | LC
RGes | 1
2

á

gedämpfte Schwingung

Daraus ergibt sich eine Richtlinie zur Dimensionierung von R und C:

R ≈ RL

2

4

RGes

L
C ≥

Der Abschaltvorgang ist in einem Oszillogramm zu dokumentieren und zwar Uce und der Strom durch das RC Glied.

## 2 Theoretische Grundlagen

Schalten bei Induktiver Last:

Beim Abschalten von Induktivitäten entstehen hohe Abschaltspannungen. Deshalb muss eine Diode als Spannungsbegrenzung parallel geschaltet werden.

Freilaufdiode

Im leitenden Zustand baut sich durch den Stromfluß in der Spule ein Magnetfeld auf, das beim Ausschalten schlagartig zusammenbricht. Die Spule versucht nun die abgeschaltete Spannung zu erhalten und erzeugt eine Induktionsspannung.
Verwendung findet diese Diode parallel zu einem Relais, das bei sperrendem Transistor eine hohe Induktionsspannung erzeugt. Die Diode fungiert hier als Schutzdiode. Die Diode schliesst die Induktionsspannung kurz und begrenzt sie auf den Wert der Diodendurchflussspannung. Nachteil dieser Methode ist allerdings eine erhöhte Abfallverzögerung des Relais.


E–Labor | Schutzbeschaltungen | 3

## 3 Schaltung

## 4 Messergebnisse

Siehe graphische Auswertung

## 5 Berechnungsbeispiele zu den Messungen

keine

E–Labor | Schutzbeschaltungen | 4

## 6 Grafische Auswertung

Der Strom wird über einen Messumformer gemessen.
ACHTUNG: 1 Volt in der Schaltung sind 100 mV am Oszilloskop!

Eingangssignal (vom Frequenzgenerator):

Eingangs-Signal

Skalierung: 2 V / Div; 500 uS


E–Labor | Schutzbeschaltungen | 5

Induktive Last mit 4 mH und 40 Ohm:

Skalierung: CH1 50 V / Div; CH2 50 mV / Div ; 10 uS

Skalierung: CH1 50 V / Div; CH2 50 mV / Div ; 500 uS

Spannung


E–Labor | Schutzbeschaltungen | 6

Induktive Last, mit Freilaufdiode:
(Strom Ic)

Skalierung: CH1 10 V / Div; CH2 50 mV / Div ; 500 uS

Induktive Last, mit Freilaufdiode:
(Strom Id)

Skalierung: CH1 10 V / Div; CH2 50 mV / Div ; 500 uS

E–Labor | Schutzbeschaltungen | 7

Induktive Last, mit Freilaufdiode:
(Strom IL)


Skalierung: CH1 10 V / Div; CH2 50 mV / Div ; 500 uS

## 7 Bewertung der Messergebnisse

Bei einer Schaltung mit induktiver Last treten ohne Schutzbeschaltung beim Abschalten hohe Spannungen auf.
Der bei Verwendung einer Freilaufdiode durch diese abfließende Strom ist anhand der aufgenommenen Bilder vom Oszilloskop gut zu erkennen und nachvollziehbar.

## 8 Anmerkungen

Keine

E–Labor | Schutzbeschaltungen | 8

## 9 Geräteliste

Bezeichnung | Geräteart | Messwerk
-symbol

Positi
on

Messbereich/
bzw. Kennwerte Gerätenummer

Funktionsgenerator

Transistor-Test-Brett

Lastwiderstand | Rl | 40 Ohm
Induktivität | L | 4 mH
Netzgerät | | DC 0-30 V
Messverstärker | | 1 – 500 V

Oszilloskop

Datum | Unterschrift

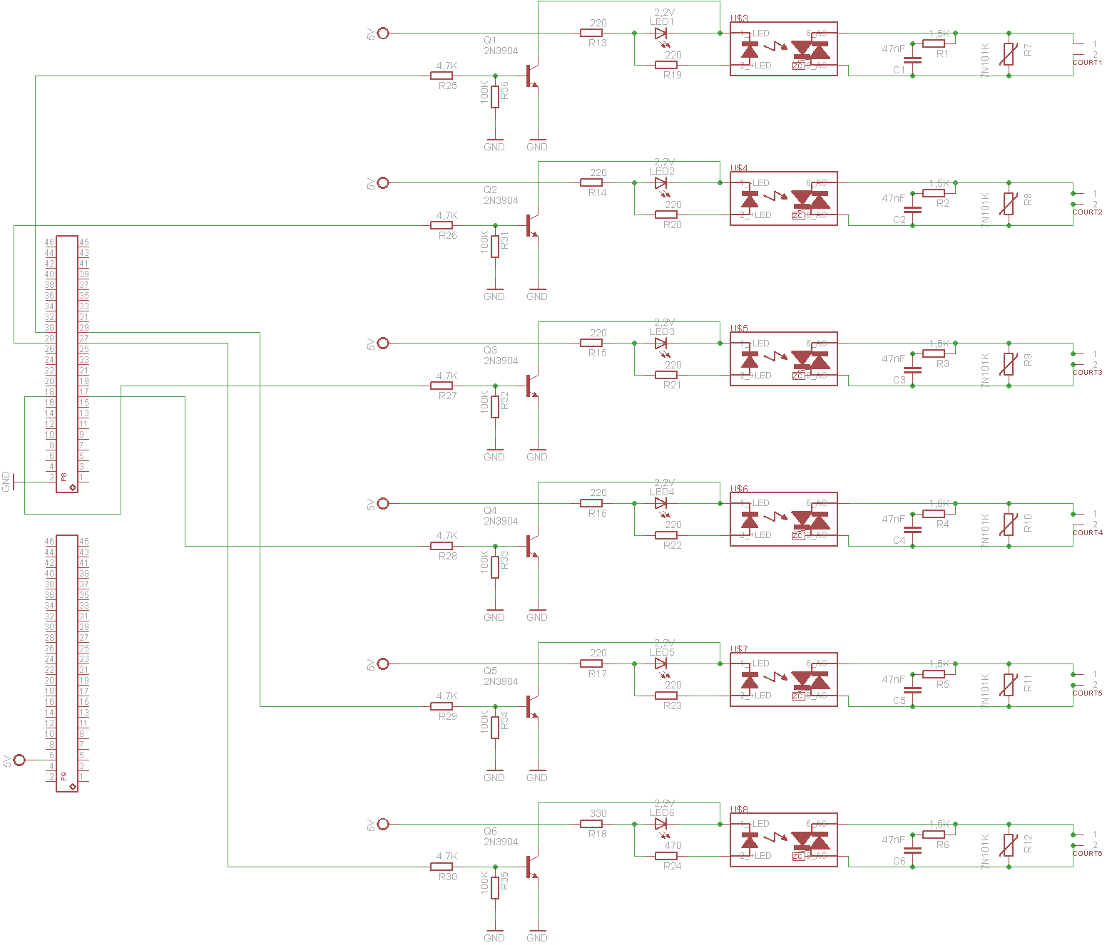
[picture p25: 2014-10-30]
Circuitry/Cape/platine_gesamt_V05sch.png

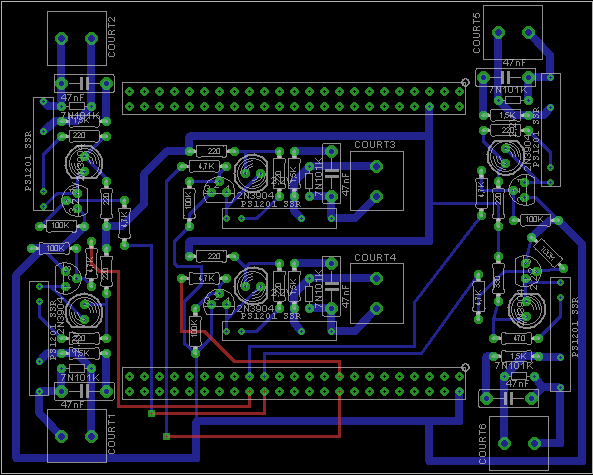
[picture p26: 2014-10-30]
Circuitry/Cape/platine_gesamt_V05brd.png

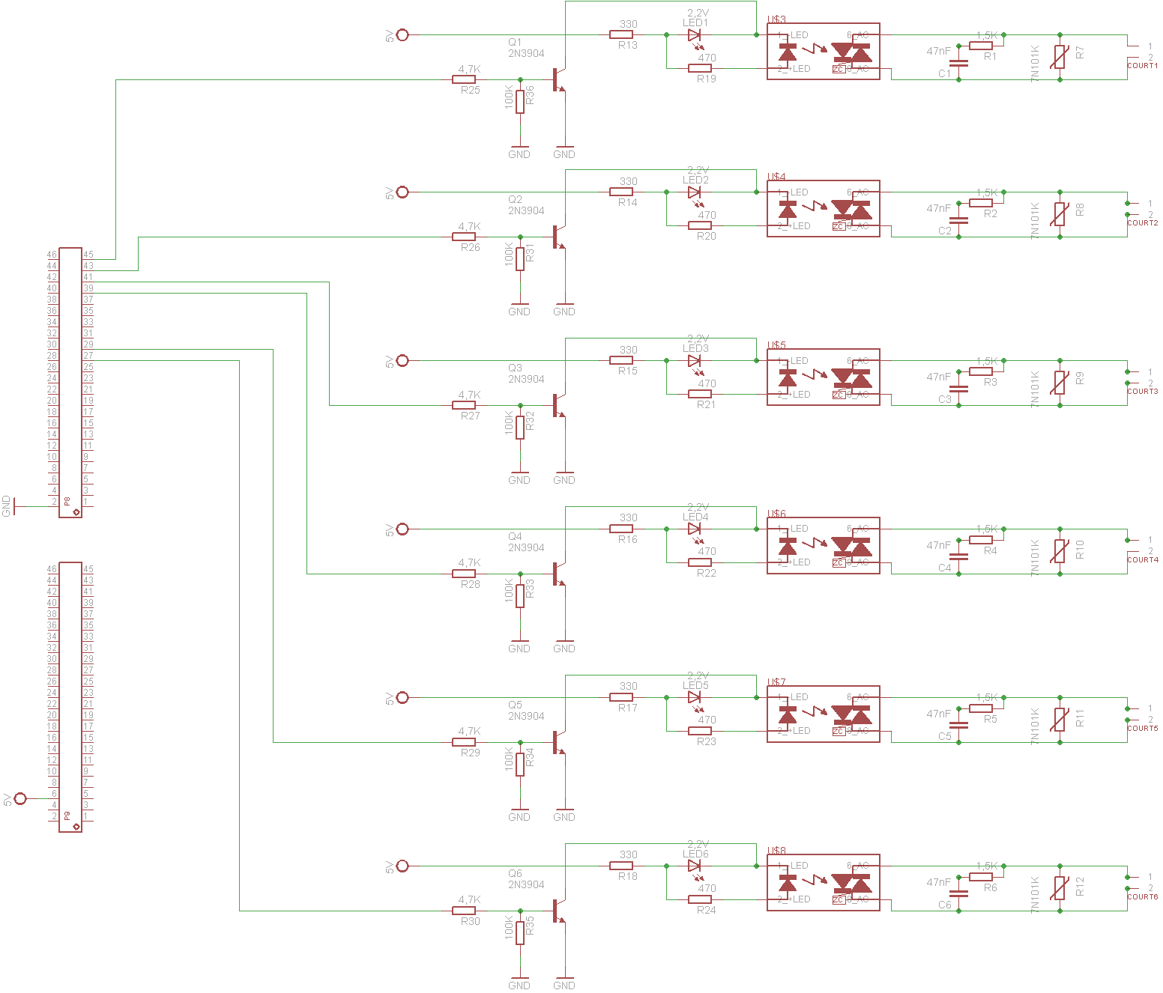
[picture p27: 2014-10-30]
Circuitry/Cape/platine_gesamt_sch_v3.png

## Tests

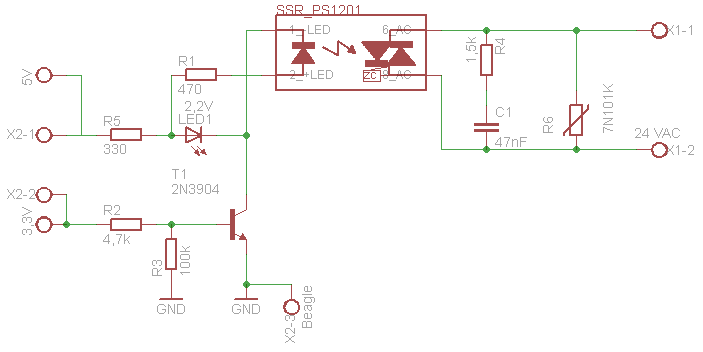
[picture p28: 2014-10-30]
Circuitry/TestBoard/ssr_ansteuerung_v7.png

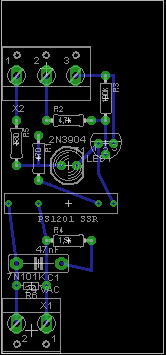
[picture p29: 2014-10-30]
Circuitry/TestBoard/tsv_relais_steuerung_layout_v7.png

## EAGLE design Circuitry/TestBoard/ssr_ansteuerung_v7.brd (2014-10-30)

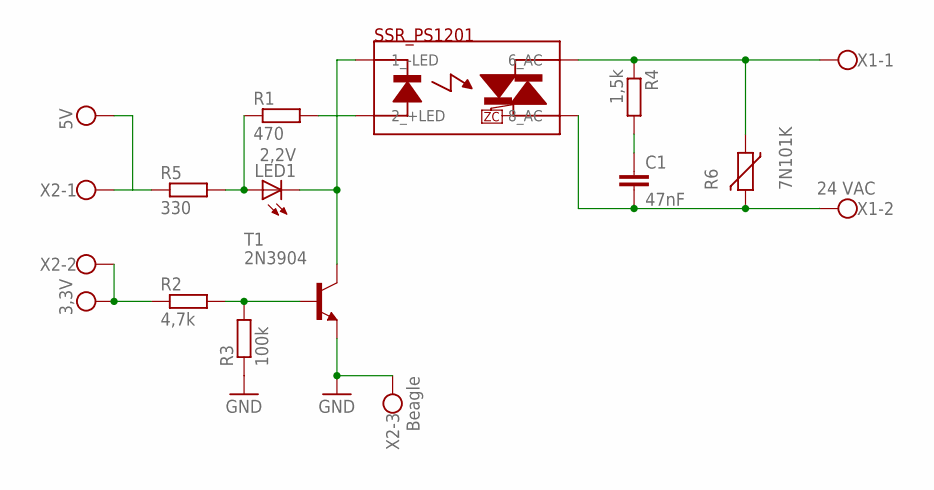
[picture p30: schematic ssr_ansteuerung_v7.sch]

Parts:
C1: 47nF; C7.5B3
LED1: 2,2V; LED5MM
R1: 470; 0204/7
R2: 4,7k; 0204/7
R3: 100k; 0204/7
R4: 1,5k; 0204/7
R5: 330; 0204/7
R6: 7N101K; R-5
SSR_PS1201: SSR PS1201; S202S02
T1: 2N3904; TO92
X1: 24 VAC; W237-102
X2: Beagle; W237-103

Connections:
GND: R3.1, T1.3 (E), X2.3
unnamed: R1.2, SSR_PS1201.2 (2_+LED)
unnamed: LED1.A, R1.1, R5.2
unnamed: R2.2, R3.2, T1.2 (B)
unnamed: LED1.K (C), SSR_PS1201.1 (1_-LED), T1.1 (C)
unnamed: C1.1, R4.2
unnamed: R4.1, R6.1, SSR_PS1201.6 (6_AC), X1.1
unnamed: C1.2, R6.2, SSR_PS1201.8 (8_AC), X1.2
unnamed: R5.1, X2.1
VCC: R2.1, X2.2

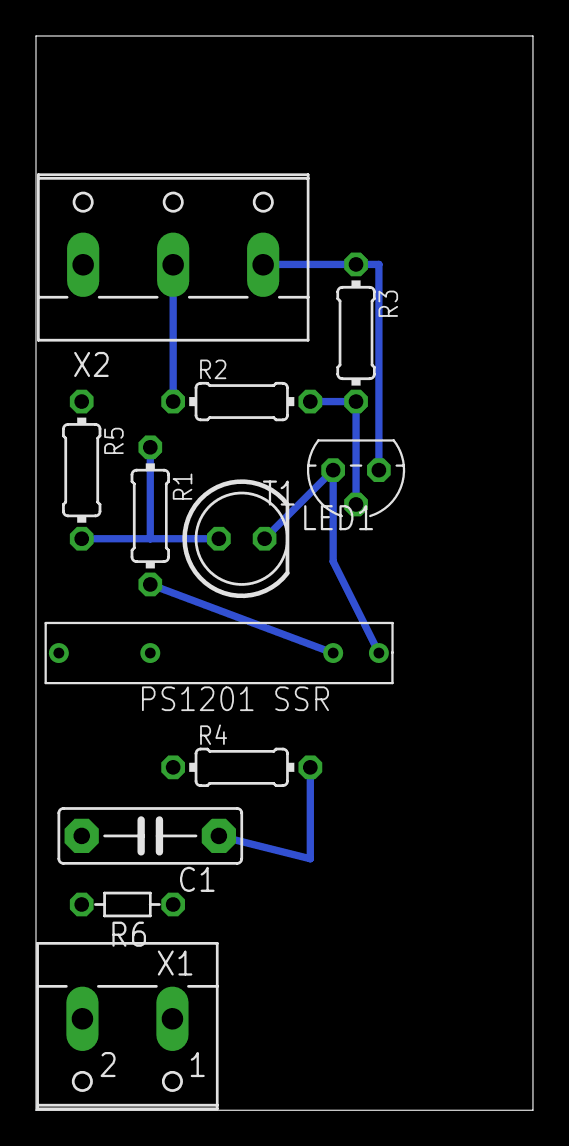
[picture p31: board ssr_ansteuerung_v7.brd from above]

Board: 2 copper layers, 27.6 x 59.7 mm, 12 parts (0 on the bottom side), 10 nets.

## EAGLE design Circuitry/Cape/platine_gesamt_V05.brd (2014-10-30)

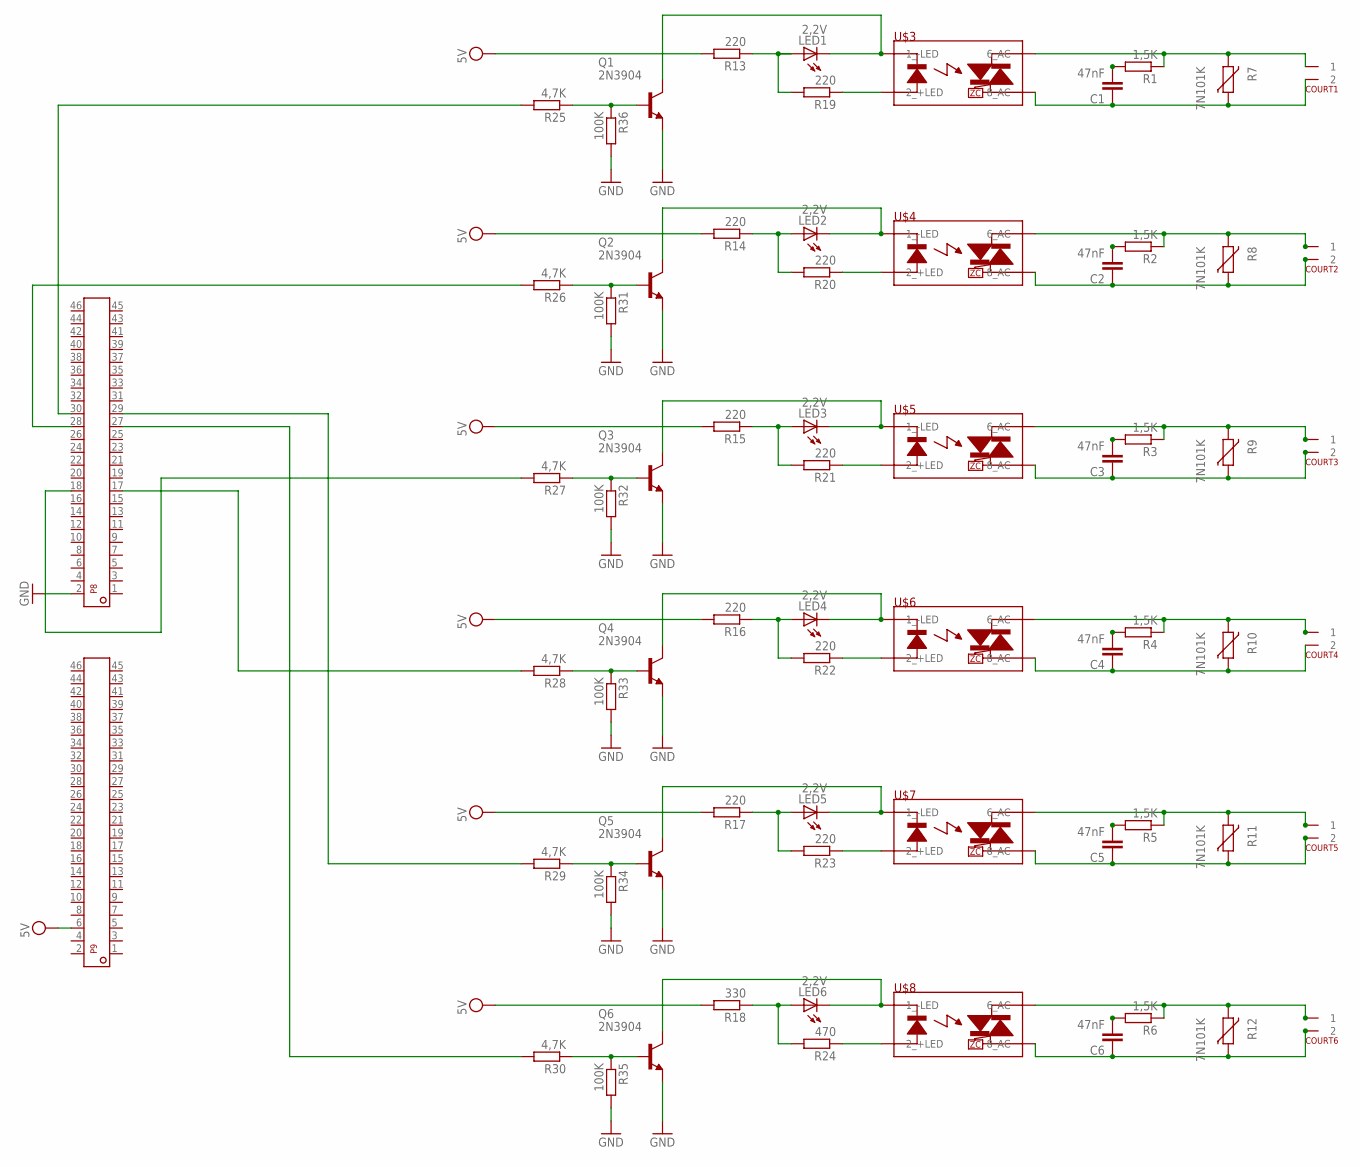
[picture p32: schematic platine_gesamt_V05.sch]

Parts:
C1, C2, C3, C4, C5, C6: 47nF; C7.5B3
COURT1, COURT2, COURT3, COURT4, COURT5, COURT6: KLEMMENBLOCK_2POL
LED1, LED2, LED3, LED4, LED5, LED6: 2,2V; LED5MM
P8, P9: FEMALE_HEADER_2X23; FE23-2W
Q1, Q2, Q3, Q4, Q5, Q6: 2N3904; TO92
R1, R2, R3, R4, R5, R6: 1,5K; 0204/7
R7, R8, R9, R10, R11, R12: 7N101K; R-5
R13, R14, R15, R16, R17, R19, R20, R21, R22, R23: 220; 0204/7
R18: 330; 0204/7
R24: 470; 0204/7
R25, R26, R27, R28, R29, R30: 4,7K; 0204/7
R31, R32, R33, R34, R35, R36: 100K; 0204/7
U$3, U$4, U$5, U$6, U$7, U$8: IXYS_PS1201_SSRSIP4/8; S202S02

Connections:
GND: P8.2, Q1.3 (E), Q2.3 (E), Q3.3 (E), Q4.3 (E), Q5.3 (E), Q6.3 (E), R31.2, R32.2, R33.2, R34.2, R35.2, R36.2
unnamed: C1.2, R1.2
unnamed: C2.2, R2.2
unnamed: C3.2, R3.2
unnamed: C4.2, R4.2
unnamed: C5.2, R5.2
unnamed: C6.2, R6.2
unnamed: COURT1.1, R1.1, R7.2, U$3.6 (6_AC)
unnamed: P8.18, R27.2
unnamed: C2.1, COURT2.2, R8.1, U$4.8 (8_AC)
unnamed: C3.1, COURT3.2, R9.1, U$5.8 (8_AC)
unnamed: C4.1, COURT4.2, R10.1, U$6.8 (8_AC)
unnamed: C5.1, COURT5.2, R11.1, U$7.8 (8_AC)
unnamed: C6.1, COURT6.2, R12.1, U$8.8 (8_AC)
unnamed: COURT2.1, R2.1, R8.2, U$4.6 (6_AC)
unnamed: COURT3.1, R3.1, R9.2, U$5.6 (6_AC)
unnamed: COURT4.1, R4.1, R10.2, U$6.6 (6_AC)
unnamed: COURT5.1, R5.1, R11.2, U$7.6 (6_AC)
unnamed: COURT6.1, R6.1, R12.2, U$8.6 (6_AC)
unnamed: LED1.A, R13.1, R19.2
unnamed: R19.1, U$3.2 (2_+LED)
unnamed: LED1.K (C), Q1.1 (C), U$3.1 (1_-LED)
unnamed: Q1.2 (B), R25.1, R36.1
unnamed: LED2.A, R14.1, R20.2
unnamed: R20.1, U$4.2 (2_+LED)
unnamed: LED2.K (C), Q2.1 (C), U$4.1 (1_-LED)
unnamed: Q2.2 (B), R26.1, R31.1
unnamed: LED3.A, R15.1, R21.2
unnamed: R21.1, U$5.2 (2_+LED)
unnamed: LED3.K (C), Q3.1 (C), U$5.1 (1_-LED)
unnamed: Q3.2 (B), R27.1, R32.1
unnamed: LED4.A, R16.1, R22.2
unnamed: LED4.K (C), Q4.1 (C), U$6.1 (1_-LED)
unnamed: R22.1, U$6.2 (2_+LED)
unnamed: Q4.2 (B), R28.1, R33.1
unnamed: LED5.A, R17.1, R23.2
unnamed: LED5.K (C), Q5.1 (C), U$7.1 (1_-LED)
unnamed: R23.1, U$7.2 (2_+LED)
unnamed: Q5.2 (B), R29.1, R34.1
unnamed: LED6.A, R18.1, R24.2
unnamed: LED6.K (C), Q6.1 (C), U$8.1 (1_-LED)
unnamed: R24.1, U$8.2 (2_+LED)
unnamed: Q6.2 (B), R30.1, R35.1
unnamed: P8.30, R25.2
unnamed: P8.28, R26.2
unnamed: P8.17, R28.2
unnamed: P8.29, R29.2
unnamed: P8.27, R30.2
unnamed: C1.1, COURT1.2, R7.1, U$3.8 (8_AC)
VDD: P9.6, R13.2, R14.2, R15.2, R16.2, R17.2, R18.2

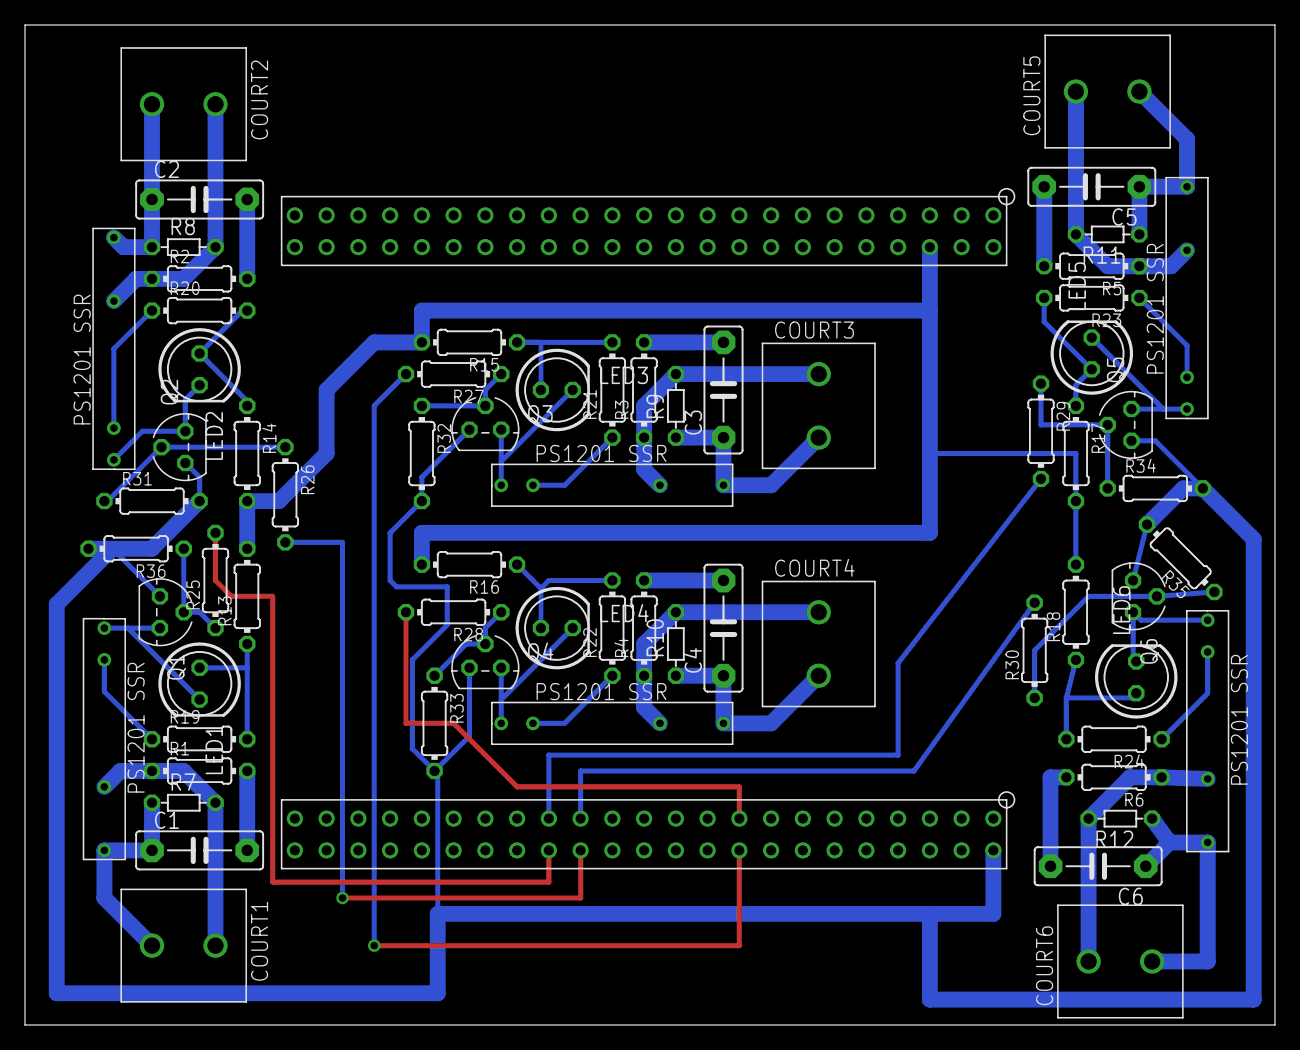
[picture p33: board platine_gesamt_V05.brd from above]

Board: 2 copper layers, 100.0 x 80.0 mm, 68 parts (0 on the bottom side), 50 nets.
